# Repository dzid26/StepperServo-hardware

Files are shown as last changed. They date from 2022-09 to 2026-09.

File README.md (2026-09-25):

## StepperServoCAN Firmware
https://github.com/dzid26/StepperServoCAN

# StepperServo-hardware
Limits:
- 3.3A peak stall current per phase for 5sec
- 3.3A RMS combined motor continuous current for >1min (i.e. rotating under load but not stalled)
- 32V supply voltage

Features:
- Intended to drive a stepper motor
- High impedance freewheeling with overvoltage protection
- Magnetic angle sensor (can be turned off during sleep)
- CANbus transceiver with standby mode
- Debug port for flashing and configuration with ESD protection
- [Low-side](https://github.com/dzid26/StepperServoCAN/pull/38) current, V_mot and V_Bat, PCB temperature measurements
- Reverse polarity protection and swapped connectors protection; ESD protections on inputs

- Optional Enable port with [Break](https://github.com/dzid26/StepperServoCAN/pull/37) interrupt capability for additional safety
- Optional expansion port for connecting UART/I2C/PWM device or a sensor (0.4A max, or 1A for v0.6)
- Optional solder jumper pads, e.g. for motor identification

## Schematic
Schematic

## PCB
- single sided PCB for direct mounting on the motor and efficient assembly
- flat bottom allows for heat dissipation and measuring motor temperature
board
case

## Motor
Motor tips:
- an examples of motor that produce a lot of torque without needing much gear ratio are Nema23 [104mm](https://www.omc-stepperonline.com/nema-23-bipolar-1-8deg-2-4nm-340oz-in-1-8a-4-95v-57x57x104mm-4-wires-23hs41-1804s) and [56mm](https://www.omc-stepperonline.com/nema-23-bipolar-1-8deg-1-16nm-164-3oz-in-1-5a-5-4v-57x57x56mm-4-wires-23hs22-1504s) - they have dense windings and high torque per amp values
- for space limited applications [this](https://www.aliexpress.com/item/4001349087963.html) coupled with single stage 5:1 gearbox can provide enough torque with relatively low friction and noise from the gearbox. Note: above 2Amps, the torque tapers off and torque ripple becomes apparent!
- rated current should not be exceeded by a lot to avoid torque ripple, motor inefficiency and overheating
- motors with high rated-current (less but thicker winding) can be used to avoid torque ripple problem, provided they are geared enough to generate enough output torque - however large gear ratios can be more prone to backlash and low efficiency which adds to backdrivinility friction
- generally big motors will have smoothest torque and don't need that much gearing

## Angle sensor magnet
- requires diametrically magnetized disk magnet
- Attaching magnet with the glue - [video](https://youtu.be/mQyXR3hITy0?t=41)
- Magnetic field [analysis](/Design/Magnet/README.md) 1-2mm thick and 5-6mm diameter magnets with about 1mm gap can be used

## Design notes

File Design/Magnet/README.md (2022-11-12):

Magnetic field plots using [Femm](https://www.femm.info/) for ⌀6x2 N38 magnet on a shaft face 3mm below PCB.
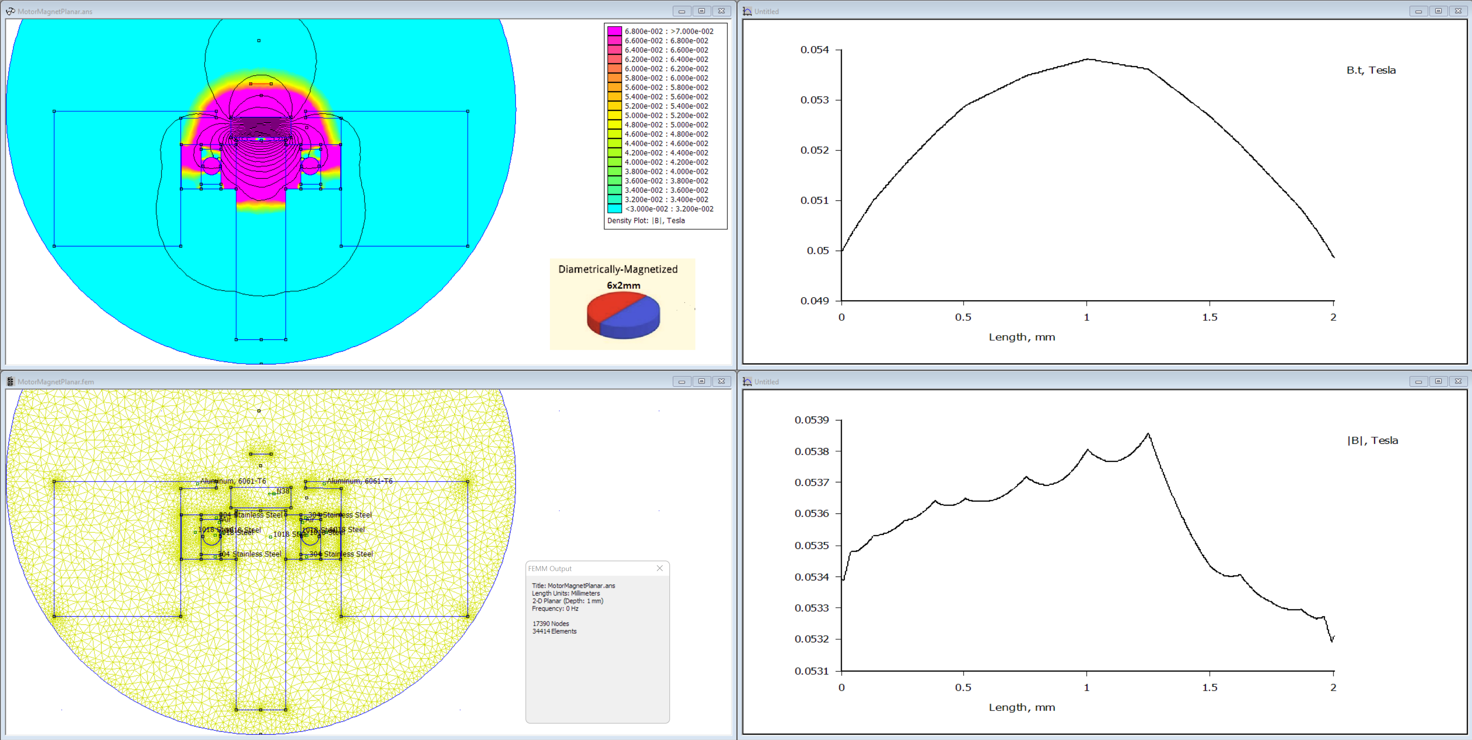
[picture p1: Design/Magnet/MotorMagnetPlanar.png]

Acceptable |B| and Bxy field ranges in the [datasheet](../../Datasheets/TLE5012B%20-%20dataheet.pdf).

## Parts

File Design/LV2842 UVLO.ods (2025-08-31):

Vbat | 12
Vstart_dcdc | 11.8
Vstop | 6
Vout | 3.36
Vena | 1.15
Ihyst | 0.000001
I1 | 0.000001
R1 | 100000
R2 | 13537.2186959031
R3 | 51000

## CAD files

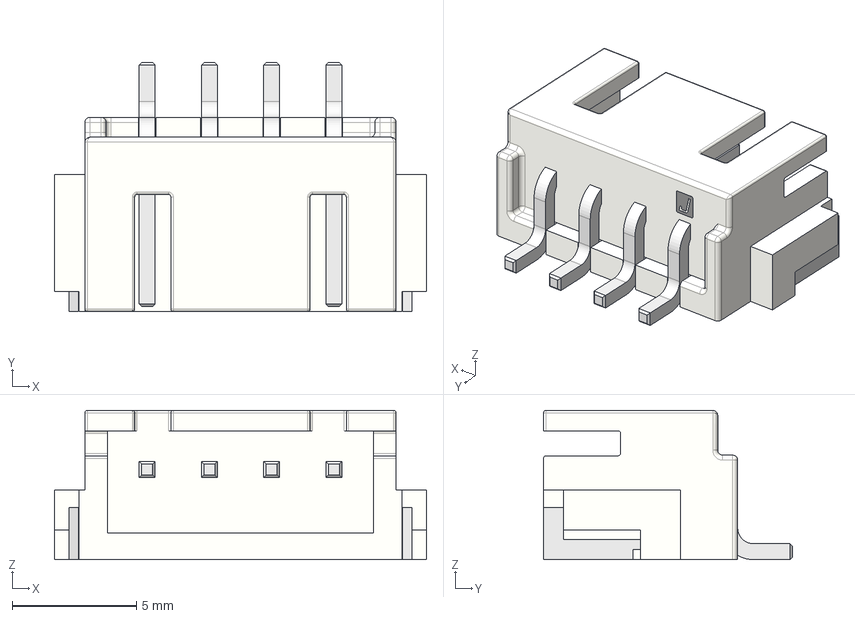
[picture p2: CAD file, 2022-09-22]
PCB/Connector_JST/Connector_JST.models/S4B-XH-SM4-TB.step
15.0 x 10.0 x 6.00 mm

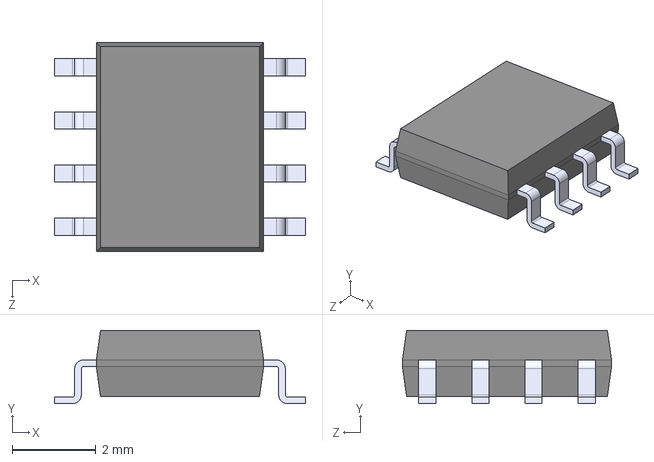
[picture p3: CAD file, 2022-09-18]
PCB/TLE5012/TLE5012.models/SOIC127P600X175-8N.step
6.00 x 1.75 x 5.00 mm

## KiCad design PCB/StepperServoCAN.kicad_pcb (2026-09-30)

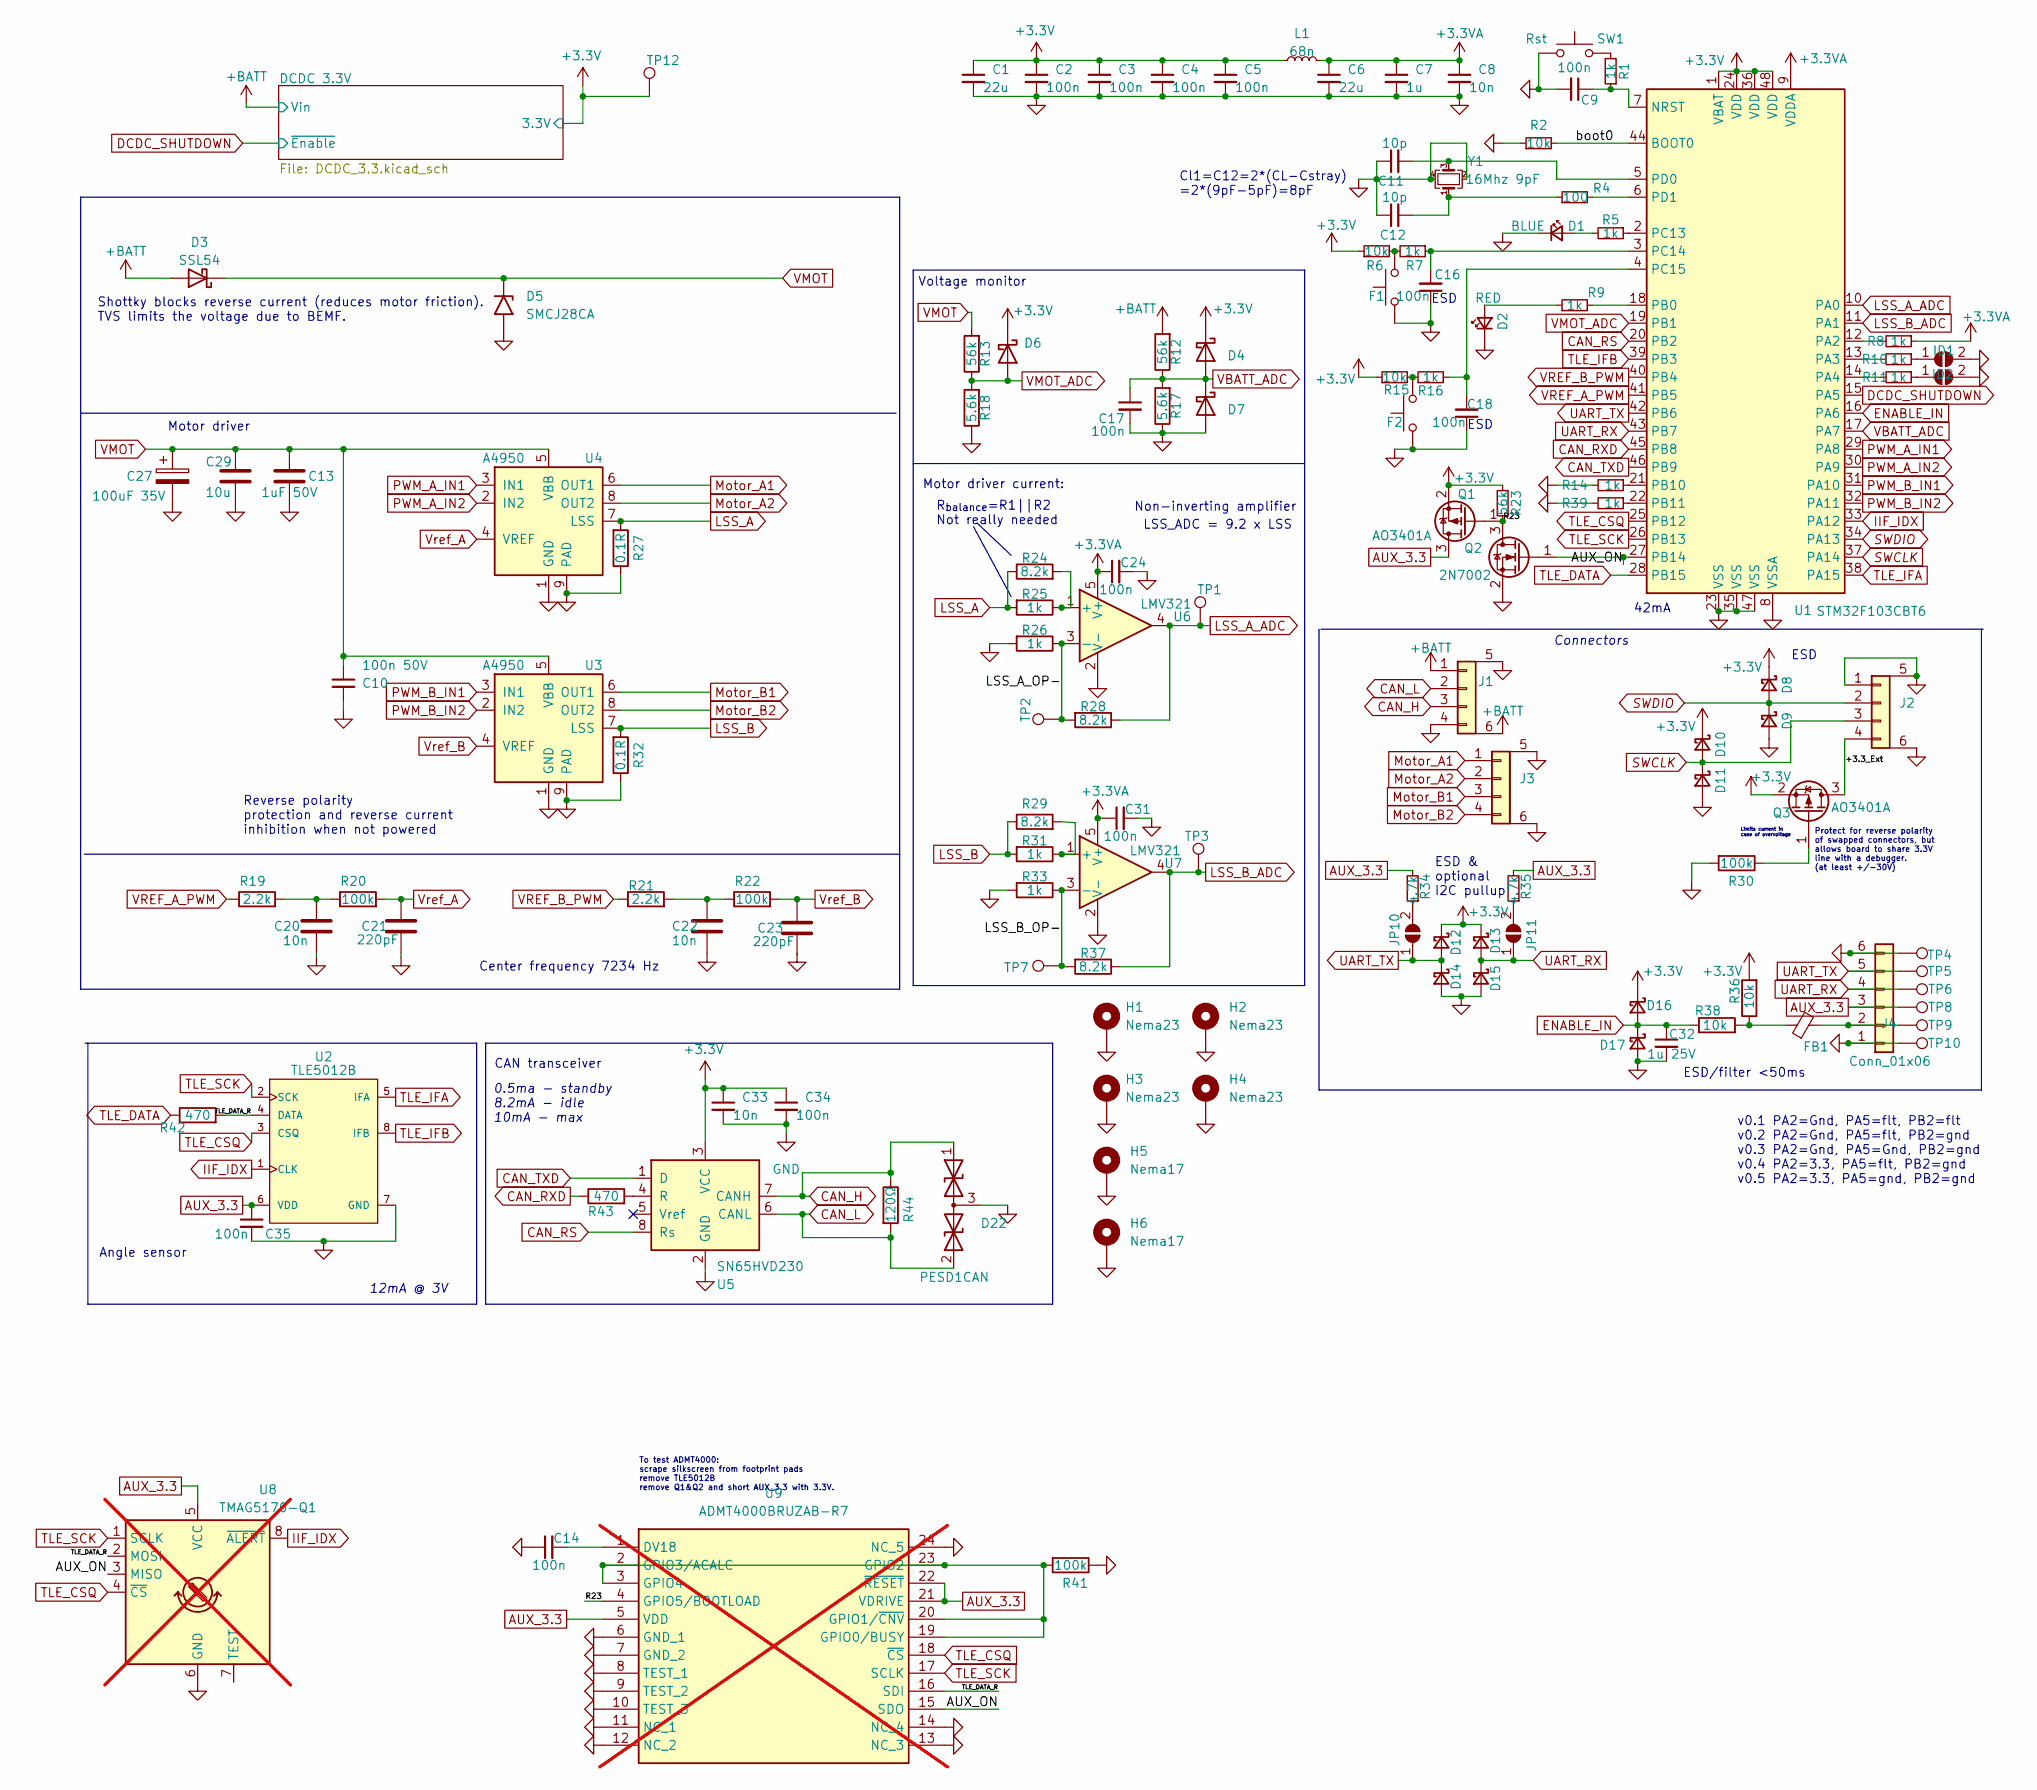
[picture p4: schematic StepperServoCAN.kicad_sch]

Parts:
C1, C6: 22u; C_0603_1608Metric; LCSC C59461
C2, C3, C4, C5, C9, C14, C16, C17, C18, C24, C31, C34, C35: 100n; C_0402_1005Metric; LCSC C1525
C7: 1u; C_0402_1005Metric; LCSC C52923
C8, C20, C22, C33: 10n; C_0402_1005Metric; LCSC C15195
C10: 100n 50V; C_0402_1005Metric; LCSC C307331
C11, C12: 10p; C_0402_1005Metric; LCSC C32949
C13: 1uF 50V; C_0805_2012Metric; LCSC C28323
C21, C23: 220pF; C_0402_1005Metric; LCSC C1530
C27: 100uF 35V; CP_Elec_6.3x5.7; LCSC C249982
C29: 10u; C_1206_3216Metric; LCSC C13585
C32: 1u 25V; C_0402_1005Metric; LCSC C52923
D1: BLUE; LED_0603_1608Metric; LCSC C2986058
D2: RED; LED_0603_1608Metric; LCSC C2286
D3: SSL54; D_SMB; LCSC C28646278
D4, D6, D7, D8, D9, D10, D11, D12, D13, D14, D15, D16, D17: 1N5819WS; D_SOD-323; LCSC C191023
D5: SMCJ28CA; D_SMC; LCSC C42371538
D22: PESD1CAN; SOT-23; LCSC C15771
F1, F2: Fcn>; SW_SPST_TL3342; LCSC C318884
FB1: FerriteBead 200mA; L_0603_1608Metric; LCSC C1002
H1, H2, H3, H4: Nema23; MountingHole_3.2mm_M3_ISO14580_Pad_TopOnly
H5, H6: Nema17; MountingHole_3.2mm_M3_ISO14580_Pad_TopOnly; LCSC C2928178
ID1, ID2: Jumper; SolderJumper-2_P1.3mm_Open_TrianglePad1.0x1.5mm
J1: CAR; JST-S4B-XH-SM4-TB; LCSC C54582908
J2: Debug; JST-S4B-XH-SM4-TB; LCSC C54582908
J3: Motor; JST-S4B-XH-SM4-TB; LCSC C54582908
J4: Conn_01x06; TerminalBlock_TE_282834-6_1x06_P2.54mm_Horizontal
JP10, JP11: I2C_PU; SolderJumper-2_P1.3mm_Open_RoundedPad1.0x1.5mm
L1: 68n; L_0603_1608Metric; LCSC C13415
Q1, Q3: AO3401A; SOT-23; LCSC C15127
Q2: 2N7002; SOT-23; LCSC C8545
R1, R5, R7, R8, R9, R10, R11, R14, R16, R25, R26, R31, R33, R39: 1k; R_0402_1005Metric; LCSC C11702
R2, R6, R15, R36, R38: 10k; R_0402_1005Metric; LCSC C25744
R4: 100; R_0402_1005Metric; LCSC C25076
R12, R13, R23: 56k; R_0402_1005Metric; LCSC C25796
R17, R18: 5.6k; R_0402_1005Metric; LCSC C25908
R19, R21: 2.2k; R_0402_1005Metric; LCSC C25879
R20, R22, R30, R41: 100k; R_0402_1005Metric; LCSC C25741
R24, R28, R29, R37: 8.2k; R_0402_1005Metric; LCSC C25924
R27, R32: 0.1R; R_1206_3216Metric_Pad1.30x1.75mm_HandSolder; LCSC C201308
R34, R35: 4.7k; R_0603_1608Metric_Pad0.98x0.95mm_HandSolder; LCSC C23162
R42, R43: 470; R_0603_1608Metric; LCSC C23179
R44: 120Ω; R_1206_3216Metric_Pad1.30x1.75mm_HandSolder; LCSC C17909
SW1: Rst; SW_SPST_TL3342; LCSC C318884
TP1, TP2, TP3, TP7: Pad; TestPoint_Pad_D1.0mm
TP4, TP5, TP6, TP8, TP9, TP10: WirePad; TestPoint_Pad_2.0x2.0mm
TP12: 3.3; TestPoint_Pad_D1.0mm
U1: STM32F103CBT6; LQFP-48_7x7mm_P0.5mm; LCSC C8734
U2: TLE5012B; Infineon-TLE5012-Level_A; LCSC C123083
U3, U4: A4950; SOIC-8-1EP_3.9x4.9mm_P1.27mm_EP2.41x3.3mm_ThermalVias; LCSC C82404
U5: SN65HVD230; SOIC-8_3.9x4.9mm_P1.27mm; LCSC C12084
U6, U7: LMV321; SOT-23-5; LCSC C7972
U8: TMAG5170-Q1; VSSOP-8_3x3mm_P0.65mm; LCSC C5220642; not fitted
U9: ADMT4000BRUZAB-R7; TSSOP-24_4.4x7.8mm_P0.65mm; not fitted
Y1: 16Mhz 9pF; Crystal_SMD_3225-4Pin_3.2x2.5mm; LCSC C13738

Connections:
+3.3V: C1.1, C2.1, C3.1, C4.1, C5.1, C33.1, C34.1, D4.1 (K), D6.1 (K), D8.1 (K), D10.1 (K), D12.1 (K), D13.1 (K), D16.1 (K), L1.1, Q1.2 (S), Q3.2 (S), R6.1, R15.1, R23.2, R36.2, TP12.1 (1_1), U1.1 (VBAT), U1.24 (VDD), U1.36 (VDD), U1.48 (VDD), U5.3 (VCC); also elsewhere on the board
+3.3VA: C6.1, C7.1, C8.1, C24.1, C31.1, L1.2, R8.1, U1.9 (VDDA), U6.5 (V+), U7.5 (V+)
+BATT: D3.2 (A), J1.1, J1.6 (Mount), R12.2; also elsewhere on the board
/+3.3_Ext: J2.4, Q3.3 (D)
/AUX_ON: Q2.1 (G), U1.27 (PB14), U8.3 (MISO), U9.15 (SDO)
/LSS_A_OP-: R26.1, R28.2, TP2.1 (1_1), U6.3 (-)
/LSS_B_OP-: R33.1, R37.2, TP7.1 (1_1), U7.3 (-)
/R23: Q1.1 (G), Q2.3 (D), R23.1, U9.4 (GPIO5/BOOTLOAD)
/TLE_DATA_R: R42.2, U2.4 (DATA), U8.2 (MOSI), U9.16 (SDI)
/boot0: R2.2, U1.44 (BOOT0)
AUX_3.3: C35.1, J4.3, Q1.3 (D), R34.2, R35.2, TP8.1 (1_1), U2.6 (VDD), U8.5 (VCC), U9.5 (VDD), U9.21 (VDRIVE), U9.22 (~RESET)
CAN_H: D22.1 (A1), J1.3, R44.1, U5.7 (CANH)
CAN_L: D22.2 (A2), J1.2, R44.2, U5.6 (CANL)
CAN_RS: U1.20 (PB2), U5.8 (Rs)
CAN_RXD: R43.1, U1.45 (PB8)
CAN_TXD: U1.46 (PB9), U5.1 (D)
DCDC_SHUTDOWN: U1.15 (PA5); also elsewhere on the board
ENABLE_IN: C32.1, D16.2 (A), D17.1 (K), R38.1, U1.16 (PA6)
GND: C1.2, C2.2, C3.2, C4.2, C5.2, C6.2, C7.2, C8.2, C9.2, C10.2, C11.1, C12.1, C13.2, C14.1, C16.1, C17.2, C18.1, C20.2, C21.2, C22.2, C23.2, C24.2, C27.2, C29.2, C31.2, C32.2, C33.2, C34.2, C35.2, D1.1 (K), D2.1 (K), D5.2 (A2), D7.2 (A), D9.2 (A), D11.2 (A), D14.2 (A), D15.2 (A), D17.2 (A), D22.3 (common), F1.2, F2.2, H1.1 (1_1), H2.1 (1_1), H3.1 (1_1), H4.1 (1_1), H5.1 (1_1), H6.1 (1_1), ID1.2 (B), ID2.2 (B), J1.4, J1.5 (Mount), J2.1, J2.5 (Mount), J2.6 (Mount), J3.5 (Mount), J3.6 (Mount), J4.1, J4.6, Q2.2 (S), R2.1, R14.2, R17.1, R18.1, R26.2, R27.1, R30.2, R32.1, R33.2, R39.2, R41.1, SW1.1, TP4.1 (1_1), TP10.1 (1_1), U1.8 (VSSA), U1.23 (VSS), U1.35 (VSS), U1.47 (VSS), U2.7 (GND), U3.1 (GND), U3.9 (PAD), U4.1 (GND), U4.9 (PAD), U5.2 (GND), U6.2 (V-), U7.2 (V-), U8.6 (GND), U9.6 (GND_1), U9.7 (GND_2), U9.8 (TEST_1), U9.9 (TEST_2), U9.10 (TEST_3), U9.11 (NC_1), U9.12 (NC_2), U9.13 (NC_3), U9.14 (NC_4), U9.24 (NC_5), Y1.2, Y1.4; also elsewhere on the board
IIF_IDX: U1.33 (PA12), U2.1 (CLK), U8.8 (~ALERT)
LSS_A: R24.1, R25.2, R27.2, U4.7 (LSS)
LSS_A_ADC: R28.1, TP1.1 (1_1), U1.10 (PA0), U6.4
LSS_B: R29.1, R31.2, R32.2, U3.7 (LSS)
LSS_B_ADC: R37.1, TP3.1 (1_1), U1.11 (PA1), U7.4
Motor_A1: J3.1, U4.6 (OUT1)
Motor_A2: J3.2, U4.8 (OUT2)
Motor_B1: J3.3, U3.6 (OUT1)
Motor_B2: J3.4, U3.8 (OUT2)
unnamed: C12.2, R4.1, Y1.1
unnamed: C20.1, R19.2, R20.1
unnamed: C22.1, R21.2, R22.1
unnamed: D1.2 (A), R5.2
unnamed: D2.2 (A), R9.1
unnamed: F1.1, R6.2, R7.2
unnamed: F2.1, R15.2, R16.1
unnamed: FB1.1, R36.1, R38.2
unnamed: ID1.1 (A), R10.1
unnamed: ID2.1 (A), R11.1
unnamed: FB1.2, J4.2, TP9.1 (1_1)
unnamed: JP10.2 (B), R34.1
unnamed: JP11.2 (B), R35.1
unnamed: Q3.1 (G), R30.1
unnamed: R1.2, SW1.2
unnamed: C9.1, R1.1, U1.7 (NRST)
unnamed: R8.2, U1.12 (PA2)
unnamed: R10.2, U1.13 (PA3)
unnamed: R11.2, U1.14 (PA4)
unnamed: R9.2, U1.18 (PB0)
unnamed: R14.1, U1.21 (PB10)
unnamed: R39.1, U1.22 (PB11)
unnamed: R5.1, U1.2 (PC13)
unnamed: C16.2, R7.1, U1.3 (PC14)
unnamed: C18.2, R16.2, U1.4 (PC15)
unnamed: C11.2, U1.5 (PD0), Y1.3
unnamed: R4.2, U1.6 (PD1)
unnamed: R43.2, U5.4 (R)
unnamed: R24.2, R25.1, U6.1 (+)
unnamed: R29.2, R31.1, U7.1 (+)
unnamed: C14.2, U9.1 (DV18)
unnamed: R41.2, U9.2 (GPIO3/ACALC), U9.3 (GPIO4), U9.19 (GPIO0/BUSY), U9.20 (GPIO1/~CNV), U9.23 (GPIO2)
PWM_A_IN1: U1.29 (PA8), U4.3 (IN1)
PWM_A_IN2: U1.30 (PA9), U4.2 (IN2)
PWM_B_IN1: U1.31 (PA10), U3.3 (IN1)
PWM_B_IN2: U1.32 (PA11), U3.2 (IN2)
SWCLK: D10.2 (A), D11.1 (K), J2.3, U1.37 (PA14)
SWDIO: D8.2 (A), D9.1 (K), J2.2, U1.34 (PA13)
TLE_CSQ: U1.25 (PB12), U2.3 (CSQ), U8.4 (~CS), U9.18 (~CS)
TLE_DATA: R42.1, U1.28 (PB15)
TLE_IFA: U1.38 (PA15), U2.5 (IFA)
TLE_IFB: U1.39 (PB3), U2.8 (IFB)
TLE_SCK: U1.26 (PB13), U2.2 (SCK), U8.1 (SCLK), U9.17 (SCLK)
UART_RX: D13.2 (A), D15.1 (K), J4.4, JP11.1 (A), TP6.1 (1_1), U1.43 (PB7)
UART_TX: D12.2 (A), D14.1 (K), J4.5, JP10.1 (A), TP5.1 (1_1), U1.42 (PB6)
VBATT_ADC: C17.1, D4.2 (A), D7.1 (K), R12.1, R17.2, U1.17 (PA7)
VMOT: C10.1, C13.1, C27.1, C29.1, D3.1 (K), D5.1 (A1), R13.2, U3.5 (VBB), U4.5 (VBB)
VMOT_ADC: D6.2 (A), R13.1, R18.2, U1.19 (PB1)
VREF_A_PWM: R19.1, U1.41 (PB5)
VREF_B_PWM: R21.1, U1.40 (PB4)
Vref_A: C21.1, R20.2, U4.4 (VREF)
Vref_B: C23.1, R22.2, U3.4 (VREF)

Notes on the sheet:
LSS_ADC = 9.2 x LSS
42mA
ESD & optional I2C pullup
R_{balance}=R1||R2 Not really needed
v0.1 PA2=Gnd, PA5=flt, PB2=flt v0.2 PA2=Gnd, PA5=flt, PB2=gnd v0.3 PA2=Gnd, PA5=Gnd, PB2=gnd v0.4 PA2=3.3, PA5=flt, PB2=gnd v0.5 PA2=3.3, PA5=gnd, PB2=gnd
CAN transceiver
Non-inverting amplifier
Center frequency 7234 Hz
Angle sensor
Protect for reverse polarity of swapped connectors, but allows board to share 3.3V line with a debugger. (at least +/-30V)
ESD
Motor driver
ESD/filter <50ms
Shottky blocks reverse current (reduces motor friction). TVS limits the voltage due to BEMF.
To test ADMT4000: scrape silkscreen from footprint pads remove TLE5012B remove Q1&Q2 and short AUX_3.3 with 3.3V.
Limits current in case of overvoltage
Connectors
12mA @ 3V
Reverse polarity protection and reverse current inhibition when not powered
Voltage monitor
0.5ma - standby 8.2mA - idle 10mA - max
Cl1=C12=2*(CL-Cstray) =2*(9pF-5pF)=8pF
Motor driver current:

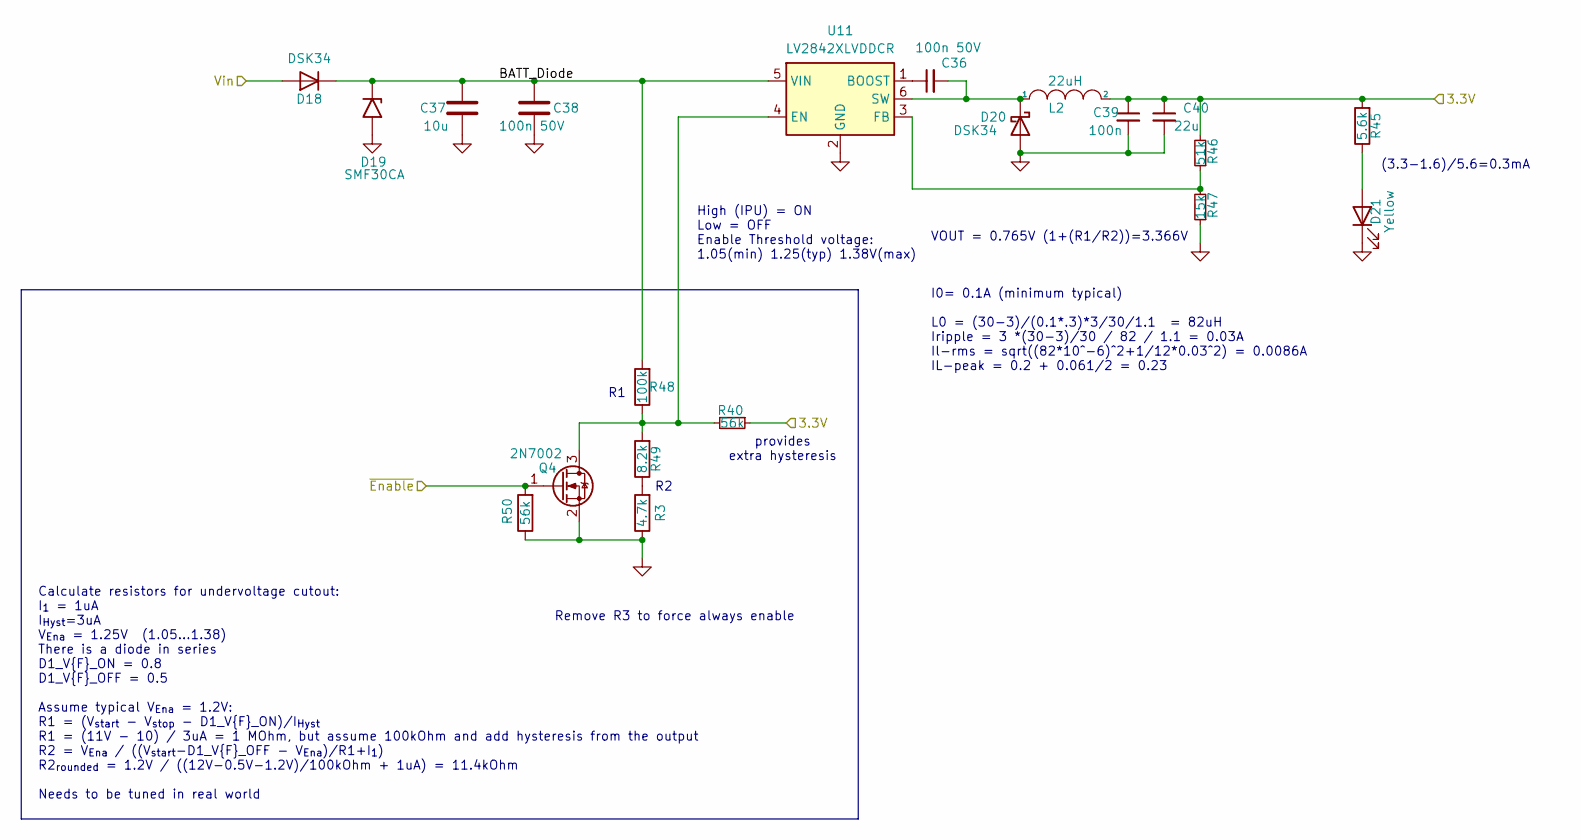
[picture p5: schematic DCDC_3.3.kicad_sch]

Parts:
C36, C38: 100n 50V; C_0402_1005Metric; LCSC C307331
C37: 10u; C_0805_2012Metric; LCSC C440198
C39: 100n; C_0402_1005Metric; LCSC C1525
C40: 22u; C_0603_1608Metric; LCSC C59461
D18, D20: DSK34; D_SOD-123F; LCSC C7502709
D19: SMF30CA; D_SMF; LCSC C19077519
D21: Yellow; LED_0603_1608Metric; LCSC C89811
L2: 22uH; L_Changjiang_FTC252010S; LCSC C5832391
Q4: 2N7002; SOT-23; LCSC C8545
R3: 4.7k; R_0402_1005Metric; LCSC C25900
R40, R50: 56k; R_0402_1005Metric; LCSC C25796
R45: 5.6k; R_0402_1005Metric; LCSC C25908
R46: 51k; R_0402_1005Metric; LCSC C25794
R47: 15k; R_0402_1005Metric; LCSC C25756
R48: 100k; R_0402_1005Metric; LCSC C25741
R49: 8.2k; R_0402_1005Metric; LCSC C25924
U11: LV2842XLVDDCR; TSOT-23-6; LCSC C225807

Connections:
+3.3V: C39.1, C40.1, L2.2, R40.1, R45.2, R46.2; also elsewhere on the board
+BATT: D18.2 (A); also elsewhere on the board
/DCDC 3.3V/BATT_Diode: C37.1, C38.1, D18.1 (K), D19.1 (A1), R48.2, U11.5 (VIN)
DCDC_SHUTDOWN: Q4.1 (G), R50.2; also elsewhere on the board
GND: C37.2, C38.2, C39.2, C40.2, D19.2 (A2), D20.2 (A), D21.1 (K), Q4.2 (S), R3.1, R47.1, R50.1, U11.2 (GND); also elsewhere on the board
unnamed: C36.2, D20.1 (K), L2.1, U11.6 (SW)
unnamed: D21.2 (A), R45.1
unnamed: Q4.3 (D), R40.2, R48.1, R49.2, U11.4 (EN)
unnamed: R3.2, R49.1
unnamed: C36.1, U11.1 (BOOST)
unnamed: R46.1, R47.2, U11.3 (FB)

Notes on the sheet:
provides extra hysteresis
(3.3-1.6)/5.6=0.3mA
Calculate resistors for undervoltage cutout: I_{1} = 1uA I_{Hyst}=3uA V_{Ena} = 1.25V (1.05...1.38) There is a diode in series D1_V{F}_ON = 0.8 D1_V{F}_OFF = 0.5 Assume typical V_{Ena} = 1.2V: R1 = (V_{start} - V_{stop} - D1_V{F}_ON)/I_{Hyst} R1 = (11V - 10) / 3uA = 1 MOhm, but assume 100kOhm and a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
I0= 0.1A (minimum typical) L0 = (30-3)/(0.1*.3)*3/30/1.1 = 82uH Iripple = 3 *(30-3)/30 / 82 / 1.1 = 0.03A Il-rms = sqrt((82*10^-6)^2+1/12*0.03^2) = 0.0086A IL-peak = 0.2 + 0.061/2 = 0.23
Remove R3 to force always enable
High (IPU) = ON Low = OFF Enable Threshold voltage: 1.05(min) 1.25(typ) 1.38V(max)
VOUT = 0.765V (1+(R1/R2))=3.366V

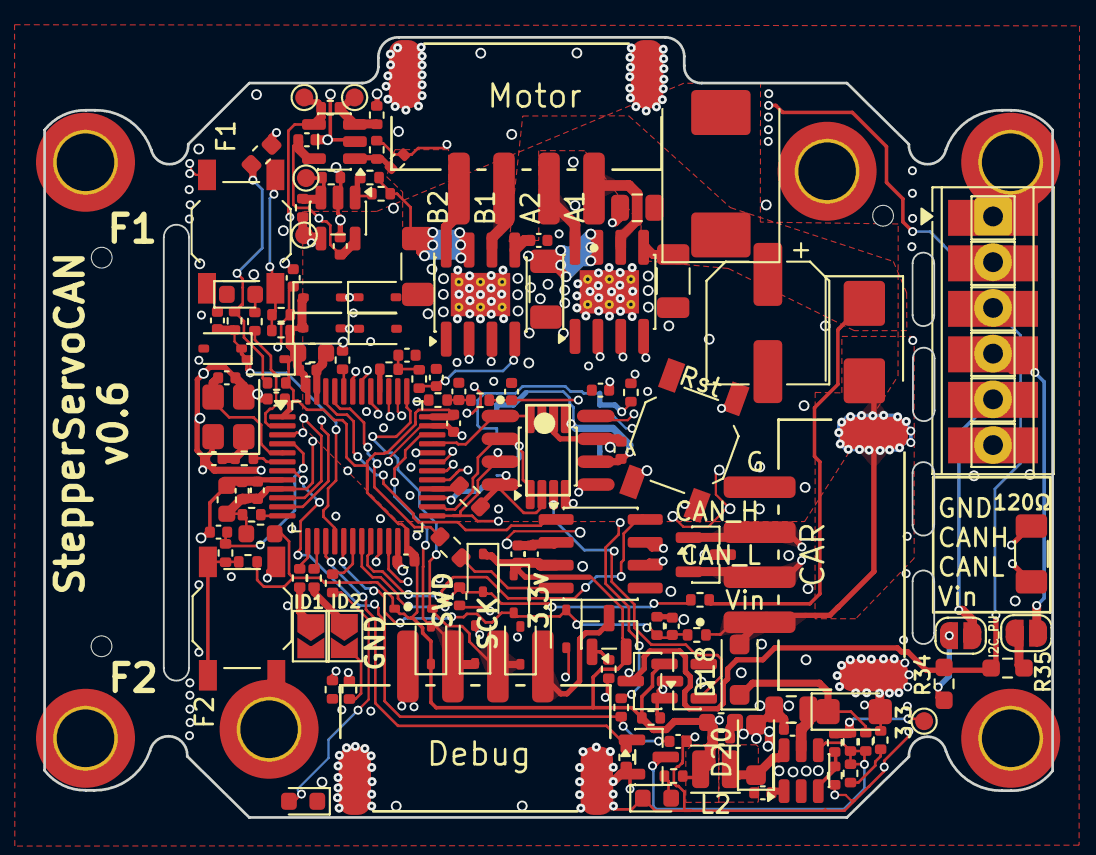
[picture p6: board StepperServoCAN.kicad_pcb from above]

Board: 4 copper layers, 56.0 x 43.3 mm, 152 parts (1 on the bottom side), 87 nets.

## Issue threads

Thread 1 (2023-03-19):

Reduce pad size for the JST connectors

dzid26, 2023-03-19:
They are too long and connectors shift a bit during assembly.

Closed 2024-08-24.

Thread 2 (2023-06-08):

LSS_A/LSS_B non-inverting amplifier ignores negative voltage?

OxygenLiu, 2023-06-08:
Depending on the forward or reverse rotation, LSS_A and LSS_B vary between -0.33 and +0.33V.

However, the OpAmp LV321 has only positive supply of +3.3V, there is no negative supply of -3.3V or voltage offset, it appears to me the negative voltage is ignored.

dzid26, 2023-06-08:
No, LSS_x  cannot be negative.
(Notice it is connected to the ground and so it can't be less than ground)
This is called [low side current sensing](https://docs.simplefoc.com/low_side_current_sense) and is much simpler (especially with this design, since the sense resistors were already there), but it only can measure current when the H-bridge is conducting current. For this reason the reading needs to be synchronized with the driver.

For current control where the A4950 chip controls the current we don't know when it is transmitting the current. So the only choice is to oversamople and measure some average current.  This can't be used for any type of control (and does need to be since the chip is in control), but could be useful for some diagnostic (basically telling whether there is current or not).

In voltage control, on which I started [working on](https://github.com/dzid26/StepperServoCAN/tree/voltage-control)  it is possible to precisely synchronize the reading.  But I haven't implemented it.

So right now the current sensing is not used.  The op amps are nice though, because thanks to the amplification,  even now if you can easily measure the current waveform with a scope (albeit with gaps when H-bridge not conducting).

Closed 2023-06-08.

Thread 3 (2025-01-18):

Nema14

valepe, 2025-01-18:
Not an issue.
Is dimensional compatible with nema14 motors?
If not, do you have plans to make a compatible version?

dzid26, 2025-01-18:
It's not and not planned.

You could make an adapter though.

Closed 2025-01-18.

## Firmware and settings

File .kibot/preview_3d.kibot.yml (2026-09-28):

outputs:
  - name: 'preview_3d_top'
    comment: "raytraced 3D board view from top (PNG) for the preview release page"
    type: render_3d
    dir: img/preview3d
    options:
      # [top,bottom,front,rear,right,left,z,x,y] Point of view
      view: top
      # *Name for the generated image file (%i='$VIEW' %x='png'/'jpg')
      output: '%f-3d-top.%x'
      # [png,jpg] Output format
      format: 'png'
      # *Enable the ray tracing. Much better result, but slow
      ray_tracing: true
      # Transparent background (kicad-cli `--background transparent`).
      # Only meaningful for PNGs; the board floats without a floor.
      transparent_background: true
      # Image width (approx.)
      width: 1280
      # Image height (approx.)
      height: 720

  - name: 'preview_3d_bottom'
    comment: "raytraced 3D board view from bottom (PNG, orthographic) for the preview release page"
    type: render_3d
    dir: img/preview3d
    options:
      view: bottom
      output: '%f-3d-bottom-ortho.%x'
      format: 'png'
      # Ray tracing restored (shadows): the flat `--quality basic` render
      # left large white silk areas featureless against the white release
      # page. Prior raytraced setting per 0888845 (`ray_tracing: true`);
      # flattened to `false` in 1e30e06 — user prefers shadows.
      ray_tracing: true
      transparent_background: true
      # Flat projection for the bottom view (no perspective): cleaner for
      # inspection and pairs well with the perspective hero shot on top.
      # Only the bottom view uses it; top stays perspective.
      orthographic: true
      width: 1280
      height: 720

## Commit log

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2022-09-21 Revised capacitor package sizes due to DC bias. Added VDD decoupling capacitors and VDDA filter.
    [StepperServoCAN.kicad_sch]
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2022-09-22 LM317 reverse diode
    [StepperServoCAN.kicad_sch]
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2022-09-23 Initial layout. Footprints fixes.
    [StepperServoCAN.kicad_pcb, StepperServoCAN.kicad_sch]
2022-09-23 Debug port wrong insertion protection. LM317 adj pin filtering.
    [StepperServoCAN.kicad_pcb, StepperServoCAN.kicad_sch]
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2022-09-27 Added P-Mosfet reverse polarity protection for the motor
    [StepperServoCAN.kicad_sch]
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2022-09-29 Fixed fottprint ids. Routing. V-cut on edge layer. DRC exclusions
    [StepperServoCAN.kicad_pcb, StepperServoCAN.kicad_sch]
2022-09-29 OP-amp reconfigured to non-inverting amplification with compensation resistor and 9.2 gain to avoid clipping
    [StepperServoCAN.kicad_pcb, StepperServoCAN.kicad_sch]
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2022-10-01 DCDC power. . Analog +3.3 netrouted to op amps. Added backup power. Added test vias and spare caps.
    [StepperServoCAN.kicad_pcb, StepperServoCAN.kicad_sch]
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2022-10-02 Added CAN RXD current limiting resistor for sleep state.
    [StepperServoCAN.kicad_pcb, StepperServoCAN.kicad_sch]
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2022-10-04 Zenner diode to protect gate of reverse polarity mosfets. Extra DCDC caps.
    [StepperServoCAN.kicad_pcb, StepperServoCAN.kicad_sch]
2022-10-05 3.3v DCDC. Bigger coil for small currents. Removed LDO. Rearranged. Optimized power traces widths.
    [StepperServoCAN.kicad_pcb, StepperServoCAN.kicad_sch]
2022-10-05 10uF 0402 decoupling -> 22uF 0603. Optimized track widths
    [StepperServoCAN.kicad_pcb, StepperServoCAN.kicad_sch]
2022-10-12 Mosfet bemf overvoltage protection. Solder jumpers, extra LED. Mov ed analog inputs. DRC.
    [StepperServoCAN.kicad_pcb, StepperServoCAN.kicad_sch]
2022-10-12 VMOT_ADC - removed protection zener and 2x resolution on voltage divider.
    [StepperServoCAN.kicad_pcb, StepperServoCAN.kicad_sch]
2022-10-13 Moved jst footprint anchor. Removed second shunts from bom. Refreshed nets.
    [StepperServoCAN.kicad_pcb]
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2022-11-29 Swapped red/blue LED. Rearranged related tracks.
    [StepperServoCAN.kicad_pcb, StepperServoCAN.kicad_sch]
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2022-12-17 Moved JST connector reference point so that actual connector sticks out more after manufacturing
    [StepperServoCAN.kicad_pcb]
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2022-12-18 Connected TLE_IFA and TLE_IFB pins from angle sensor. Optimized routings
    [StepperServoCAN.kicad_pcb, StepperServoCAN.kicad_sch]
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2022-12-18 Removed small elements silk screen designators. Cleaned up vias
    [StepperServoCAN.kicad_pcb]
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2022-12-19 Moved magnet inspection coutout for possibly better visibility
    [StepperServoCAN.kicad_pcb]
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2022-12-20 Removed thermal relief from shunt resistors for heat dissipation and from connector anchors to be stronger
    [StepperServoCAN.kicad_pcb]
2023-01-02 Mosfets replaced with Shottky and TVS.
    [StepperServoCAN.kicad_pcb, StepperServoCAN.kicad_sch]
2023-01-02 V_mot - voltage divider use higher values for less heat.
    [StepperServoCAN.kicad_pcb, StepperServoCAN.kicad_sch]
2023-01-04 Added copper under DCDC inductor and diode for better heat transfer in case of 3.3v short
    [StepperServoCAN.kicad_pcb]
2023-01-04 Back to thinner V_bat trace for better EMI
    [StepperServoCAN.kicad_pcb]
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2023-01-23 Added Enable/break pin with a filter. Repinned motor driver to Tim1.
    [StepperServoCAN.kicad_pcb, StepperServoCAN.kicad_sch]
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2023-01-24 Added extra Schottky ESD protection to Enable in
    [StepperServoCAN.kicad_pcb, StepperServoCAN.kicad_sch]
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2023-01-24 Added pull up on button RC filter for quicker charge on startup
    [StepperServoCAN.kicad_pcb, StepperServoCAN.kicad_sch]
2023-01-25 Pulled down unused pins. Added UART pads just in case
    [StepperServoCAN.kicad_pcb, StepperServoCAN.kicad_sch]
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2023-01-27 Fixed part numbers
    [StepperServoCAN.kicad_pcb, StepperServoCAN.kicad_sch]
2023-01-27 Enlarged exposed ground. Silkscreen fixes.
    [StepperServoCAN.kicad_pcb, StepperServoCAN.kicad_sch]
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2023-03-19 Corrected max current text
    [StepperServoCAN.kicad_pcb]
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2023-06-10 JST connector - shorter lead pads by 0.5mm
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2023-06-13 Removed sense resitor 2512 spare footprint. Board widened by 0.4mm
    [StepperServoCAN.kicad_pcb]
2023-06-13 Updated footprints from kicad library (rounded pads). Added more small vias for the fets. DRC fixes
    [StepperServoCAN.kicad_pcb]
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2023-06-13 Replaced 0.2mm tracks with 0.15mm. Removed rx/tx testpoints
    [StepperServoCAN.kicad_pcb, StepperServoCAN.kicad_sch]
2023-06-13 Tighter DCDC off state loop
    [StepperServoCAN.kicad_pcb]
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2023-06-14 Added VBATT_ADC protection agains large negative and positive voltages
    [StepperServoCAN.kicad_pcb, StepperServoCAN.kicad_sch]
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2023-06-15 Tighter bottom layer routing
    [StepperServoCAN.kicad_pcb, StepperServoCAN.kicad_sch]
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2023-06-15 DCDC 30V TVS extra protection. Enable pin TVS on the MCU side.
    [StepperServoCAN.kicad_pcb, StepperServoCAN.kicad_sch]
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2023-06-24 Added more powerfull CAN terminator resistor. Uses handsolder pad.
    [StepperServoCAN.kicad_pcb, StepperServoCAN.kicad_sch]
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2023-06-25 Packed DC-DC into a subsystem/ Added tap points to opamps
    [StepperServoCAN.kicad_pcb, StepperServoCAN.kicad_sch]
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2023-06-27 New DC/DC with efficient low current mode. Higher switch freq - smaller footprint.
    [DCDC_3.3.kicad_sch, StepperServoCAN.kicad_pcb, StepperServoCAN.kicad_sch]
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2023-06-28 4 layer PCB. Routing optimizations on top layer. Inner layers are plane grounds for better thermals and also EMI.
    [StepperServoCAN.kicad_pcb]
2023-06-29 Added Vgs protection for debug port reverse polarity protection mosfet.
    [StepperServoCAN.kicad_pcb, StepperServoCAN.kicad_sch]
2023-06-29 Stronger reverse polarity protection mosfet
    [StepperServoCAN.kicad_sch]
2023-06-29 Removed back zener from reverse polarity mosfet as it's not needed.
    [StepperServoCAN.kicad_pcb, StepperServoCAN.kicad_sch]
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2023-06-29 Schootky reverse voltage protection replaced with switching diode to make there is no reverse current
    [DCDC_3.3.kicad_sch, StepperServoCAN.kicad_pcb]
2023-06-30 P-channel aux load switching pullup (normally opened). Optional disabling of DCDC
    [DCDC_3.3.kicad_sch, StepperServoCAN.kicad_pcb, StepperServoCAN.kicad_sch]
2023-07-01 Smaller Thermal vias. Returned to slder mask in the back.
    [StepperServoCAN.kicad_pcb]
2023-07-03 Inverted bottom silkscreen to make bottom even for better heat conductivity.
    [StepperServoCAN.kicad_pcb]
2023-07-06 Mosfets for load switchiong. DCDC Enable pin. Rerouting.
    [DCDC_3.3.kicad_sch, StepperServoCAN.kicad_pcb, StepperServoCAN.kicad_sch]
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2023-07-07 Added test footprint for low power TMAG5170 sensor
    [StepperServoCAN.kicad_pcb, StepperServoCAN.kicad_sch]
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2023-07-09 1.2mm board. Wider snap tabs
    [StepperServoCAN.kicad_pcb]
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2023-08-03 Removed diode and a resistor - fixes DCDC SHDN pin. Corrected SHDN pin voltage calculation based on real threshold value
    [DCDC_3.3.kicad_sch, StepperServoCAN.kicad_pcb, StepperServoCAN.kicad_sch]
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2023-09-28 CAN tranciever moved to the left slightly, to make more space if someone needs to remove the terminator resistor.
    [StepperServoCAN.kicad_pcb]
2023-09-29 Direct ground path from sense resistor to electrolitic capacitor. Aux 3.3 path optimized.
    [StepperServoCAN.kicad_pcb]
2023-09-29 A4950 replaced with DRV8870
    [StepperServoCAN.kicad_pcb, StepperServoCAN.kicad_sch]
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2023-10-11 Fixed 3d model links for an export Added spare driver chip pads.
    [StepperServoCAN.kicad_pcb]
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2024-11-19 More powerful and lower breakdown voltage SMCJ28CA TVS. Better component placement - more ground pour. Capacitors moved away from mounting hole to avoid cracking
    [StepperServoCAN.kicad_pcb, StepperServoCAN.kicad_sch]
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2024-11-20 Thermal reliefs for JST connectors to avoid creep. Added via stitching to reinforce pads.
    [StepperServoCAN.kicad_pcb]
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2024-12-09 Larger pads for DCDC inductor for better thermal dissipation when shorted etc. Outline cleanup.
    [StepperServoCAN.kicad_pcb]
2024-12-10 Added hardware id table. Added hardware id v0.4. Currently not used. Might be used to to set thermal/current limits depending on the hardware
    [StepperServoCAN.kicad_pcb, StepperServoCAN.kicad_sch]
2024-12-12 ability to fully shutdown on low voltage. Power back on above 11V.
    [DCDC_3.3.kicad_sch, StepperServoCAN.kicad_pcb, StepperServoCAN.kicad_sch]
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2024-12-12 Reverted AT8236 back to A4950 for better current control capabilities
    [StepperServoCAN.kicad_pcb, StepperServoCAN.kicad_sch]
2024-12-13 Moved some signals to inner layer to free up top ground for better thermals
    [StepperServoCAN.kicad_pcb, StepperServoCAN.kicad_sch]
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2024-12-21 Removed dead properties. Found alternative Parts D1, D22, R27. PEDSCAN uses SOT323-3 footprint now
    [DCDC_3.3.kicad_sch, StepperServoCAN.kicad_pcb, StepperServoCAN.kicad_sch]
2024-12-21 Revert "0.865mm prepeg" Back to 0.2104 due to cost. This reverts commit 9494b9fe4c37bd1a66a87f1883a1c5a6efe1d1f9.
    [StepperServoCAN.kicad_pcb]
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2025-08-14 fixed uuids and re-updated board; silk_edge_clearance": "ignore",
    [StepperServoCAN.kicad_pcb]
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2025-08-17 fixed clearances
    [StepperServoCAN.kicad_pcb]
2025-08-17 Moved 120 resistor for easier insertion. CAN looped through the resistor. Removed some vias.
    [StepperServoCAN.kicad_pcb]
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2025-08-31 Min voltage 12V. DCDC shutdown from gpio via mosfet. Large hysteresis using 3.3V feedback resistor to avoid immediate restart if lower than 12V supply.
    [DCDC_3.3.kicad_sch, LV2842 UVLO.ods, StepperServoCAN.kicad_pcb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]
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2025-10-09 corrections and todos
    [DCDC_3.3.kicad_sch, StepperServoCAN.kicad_pcb, StepperServoCAN.kicad_sch]
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

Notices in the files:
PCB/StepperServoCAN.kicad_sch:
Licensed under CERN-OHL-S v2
